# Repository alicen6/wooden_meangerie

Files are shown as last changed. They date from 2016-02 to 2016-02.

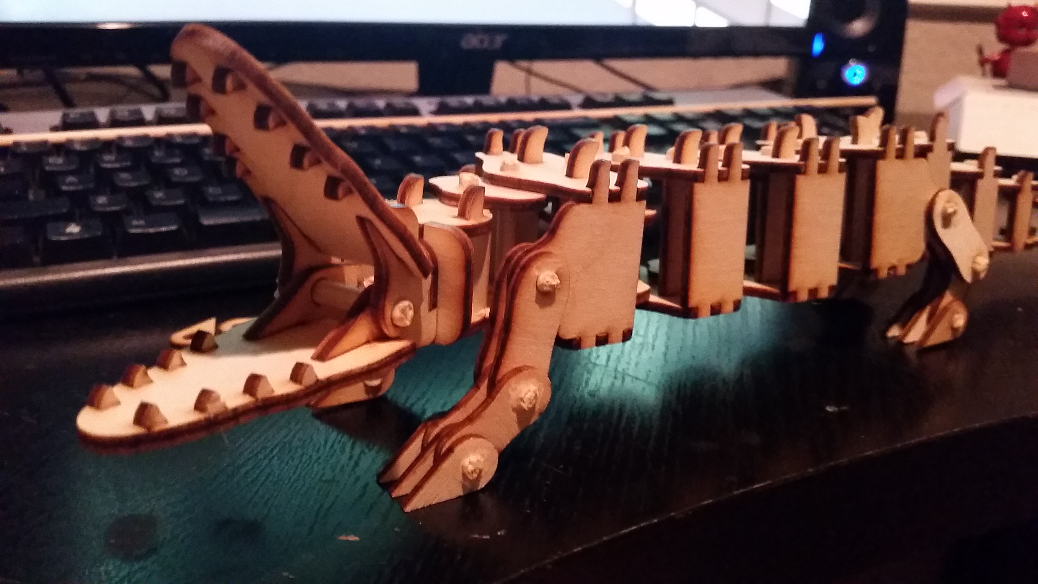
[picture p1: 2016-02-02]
images/gator.jpeg

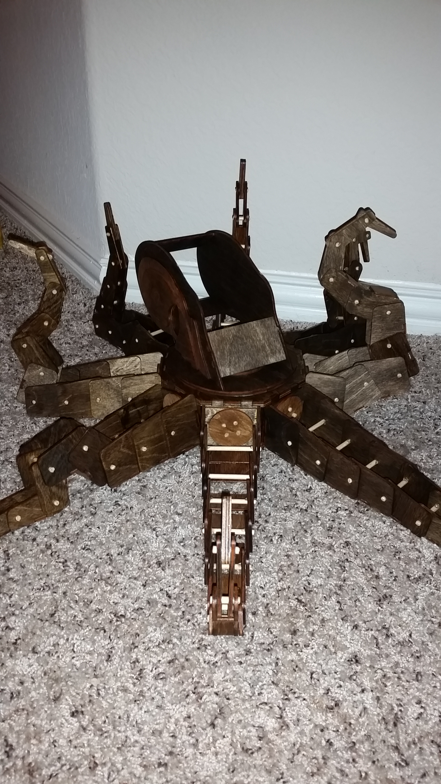
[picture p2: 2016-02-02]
images/octopus.jpg

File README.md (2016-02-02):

# Wooden Menagerie

This is a collection of files for creating articulated wooden animals. The four animals that can be created are a giraffe, an elephant, and alligator, and an octopus. All of the individual files and assemblies are within these folders.

## Materials

It is recommended to use 1/8" birch plywood or other 1/8" material for the animals. They were designed to be cut on laser cutter to reduce material waste.

The laser that they were originally created on had a bed size that would only fit 12" x 24" pieces of birch plywood, so the pre-nested files will fit onto material of that size.

These were also designed to use wooden 3/16" dowels from any Home Depot or Lowe's.

## Process

After cutting all of the pieces on a laser or other machine, it is time to assemble. For mine, I used super glue to permanently attach parts together. It is easiest to have the assembly open while putting the animal together so that you can see where different parts go.

Testing with a dry fit is encouraged, when all pieces are together, add super glue to the places that hold the dowels to keep everything together. Some areas that act as pivot points require only glue on the outer parts that touch the dowel, otherwise the pivot point won't work because they will all be glued together.

## Blog Post

http://www.alicenspurlin.com/#!Wooden-Menagerie/r2co8/5697f4e30cf20ee37c7553eb

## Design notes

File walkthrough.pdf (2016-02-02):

Wooden Menagerie Project Walkthrough

Have you ever had one of those days where you just absolutely had to make something?

I have those days far too often. I belonged to a hackerspace that had a Laser Cutter that was begging to be used. So I complied! I decided to start making articulated wooden animals that were able to be cut on the laser cutter, then assembled.

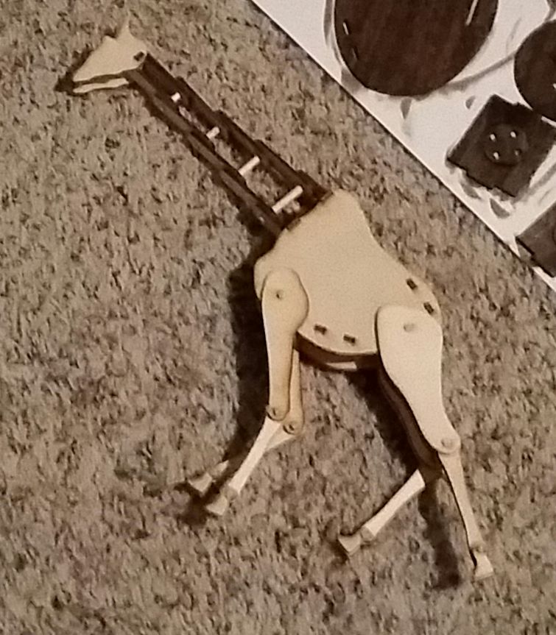
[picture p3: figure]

The first animal I began designing was a giraffe. It was fairly simple, using layers of wood to capture shafts and create joints. I used an image of a giraffe to measure and create a scale version of the animal. I also used these images to make sure that the shapes I used were accurate to the original animal.

When the pieces were cut out and I began to put them together, I found that I had made some mistakes and it didn't work as I had intended. The neck was not able to support anything and hold the head up. The pivot at the base of the head, where it connected to the neck, had not come out right in the files either.

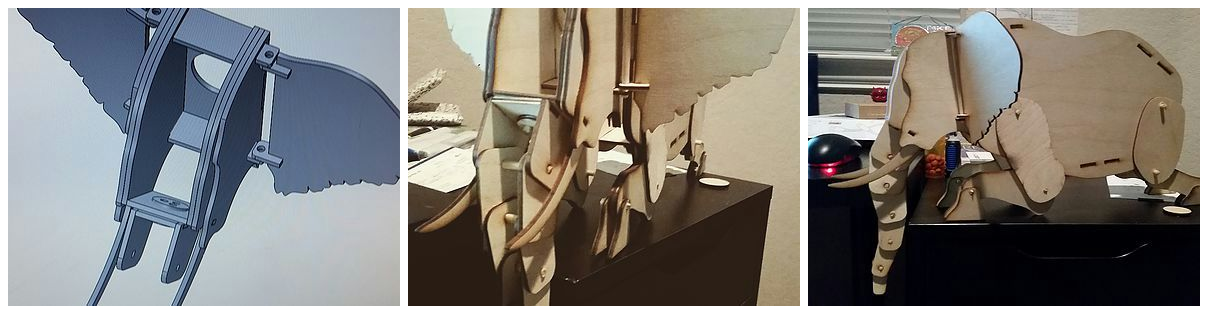
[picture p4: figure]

The second animal I designed was an elephant. The elephant was much more complex than the giraffe, with more pivots and complex build structures. The head could pivot side to side, all of the legs moved at the joints, and the ears flapped on the sides of the head. The most impressive part was the trunk, it was made of smaller and smaller sections that pivoted off one another. The trunk also pivoted at the base of the face so that it had unlimited degrees of freedom.

While assembling the elephant, the design was much more well thought out and complete, but I felt that I could still do even better.

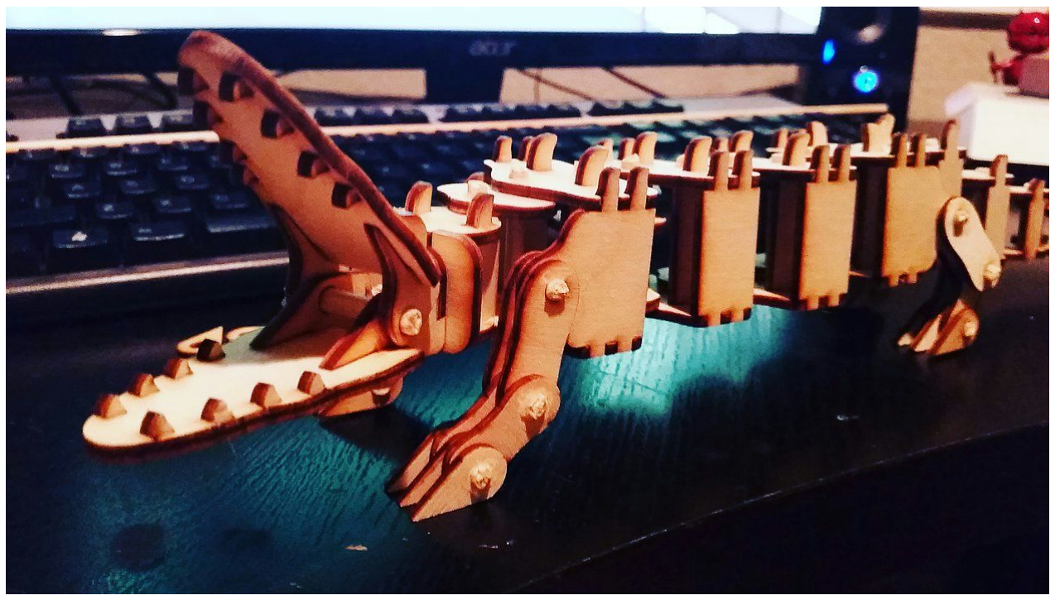
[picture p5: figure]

The third animal I designed was an alligator. The alligator was by far the most complex in the smallest package. It was made of many pieces that were similar, but would only fit together in a certain way. The entire length of the alligator was able to wiggle back and forth from the head to the tail. The legs were articulated down to the toes, and the jaw was able to open and shut.

Putting together the alligator took the longest amount of time because of the number of joints, as well as the similarity of all of the pieces.However, I still had more material I wanted to use before I moved and no longer had immediate access to the laser cutter.

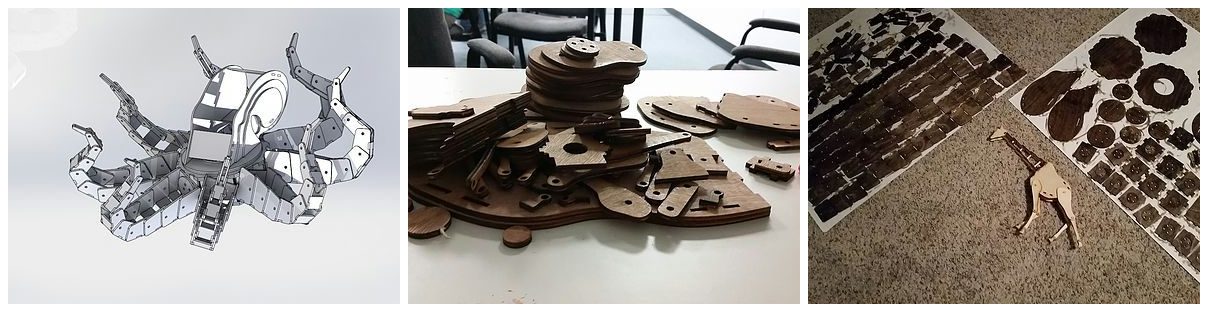
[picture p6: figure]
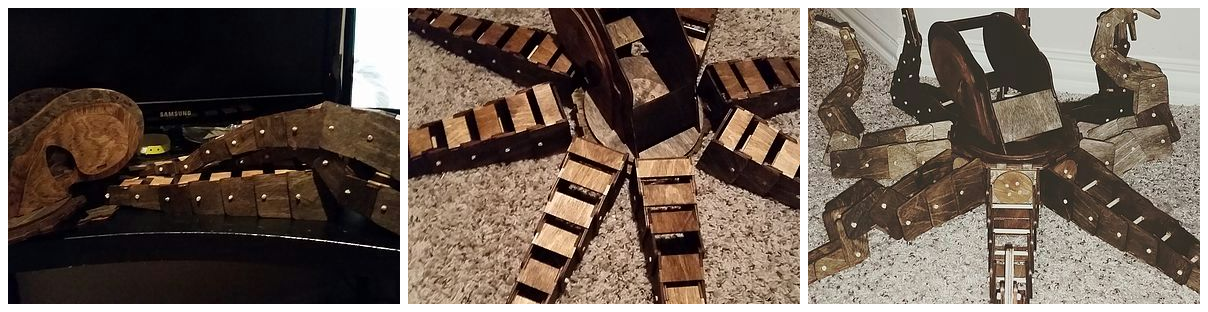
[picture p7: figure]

The fourth animal I created was an octopus. For this one, I decided to make it larger than the others. The final octopus is three feet across. The head of the octopus is able to rotate around completely. Each of the tentacles is able to rotate at the base a full 360 degrees, as well as pivot at each of the sections of the tentacles. Because I wanted to make this octopus a more finished piece than the others, I stained the parts in two different color stains before I assembled the creature together.

This project has been one of my favorites because it still has room to continue and grow, it could potentially go on forever as I learn more and more about the materials I could use and the different types of cuts and bends I can create with the laser cutter. I chose to share this project with you because I feel it shows a different side and thought process to design.

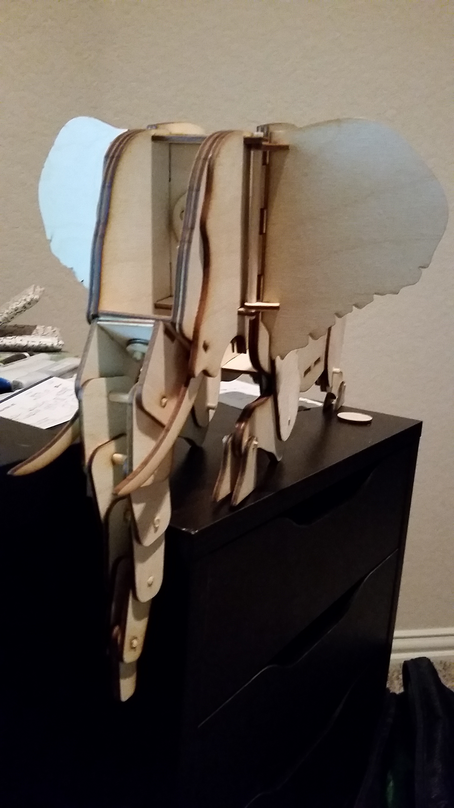
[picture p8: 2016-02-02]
images/elephant.jpg

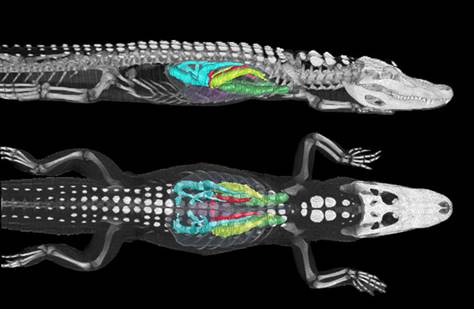
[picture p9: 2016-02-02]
alligator/alligator-CT-100114-hmed-4p.grid-6x2.jpg

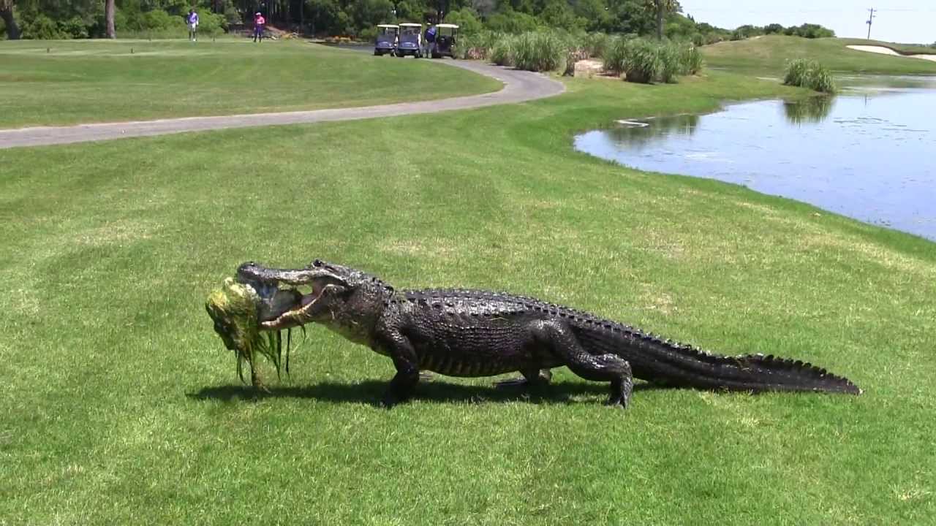
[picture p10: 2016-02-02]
alligator/maxresdefault.jpg

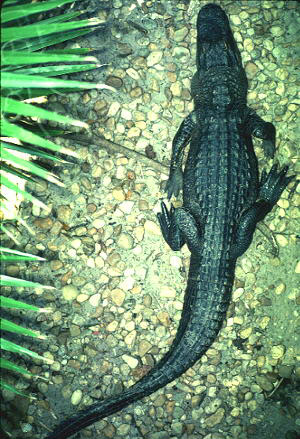
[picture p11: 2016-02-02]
alligator/!amis15.jpg

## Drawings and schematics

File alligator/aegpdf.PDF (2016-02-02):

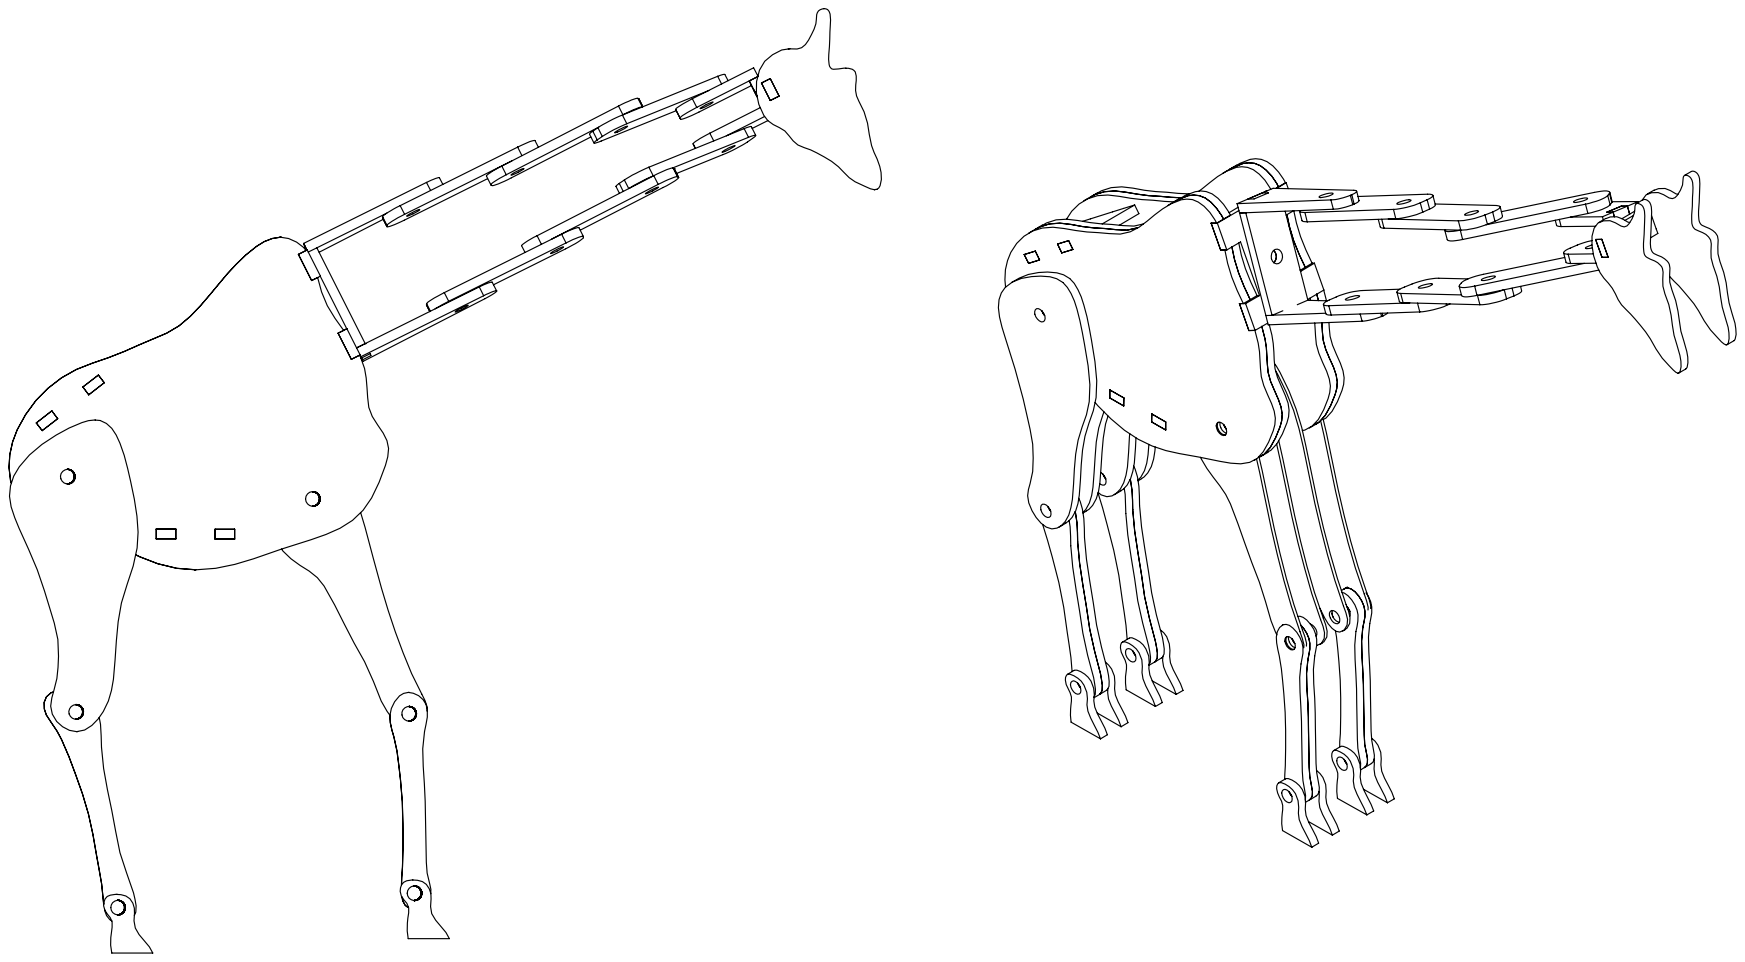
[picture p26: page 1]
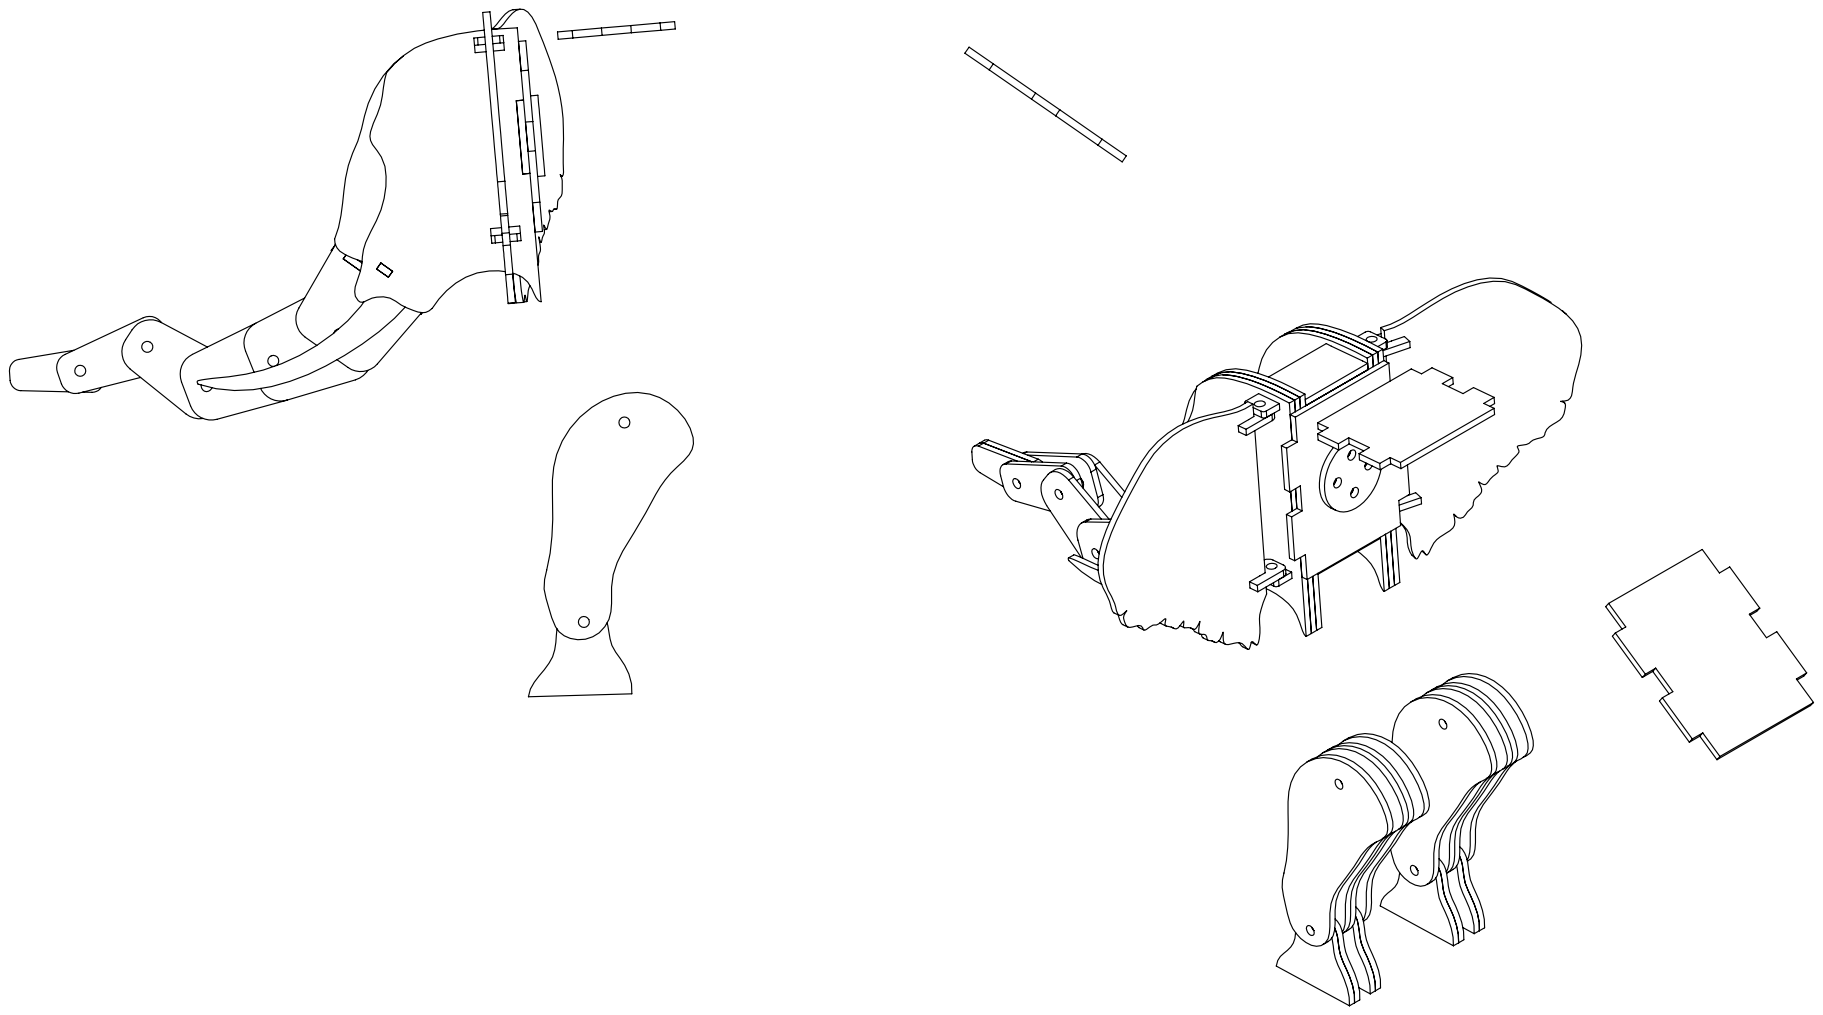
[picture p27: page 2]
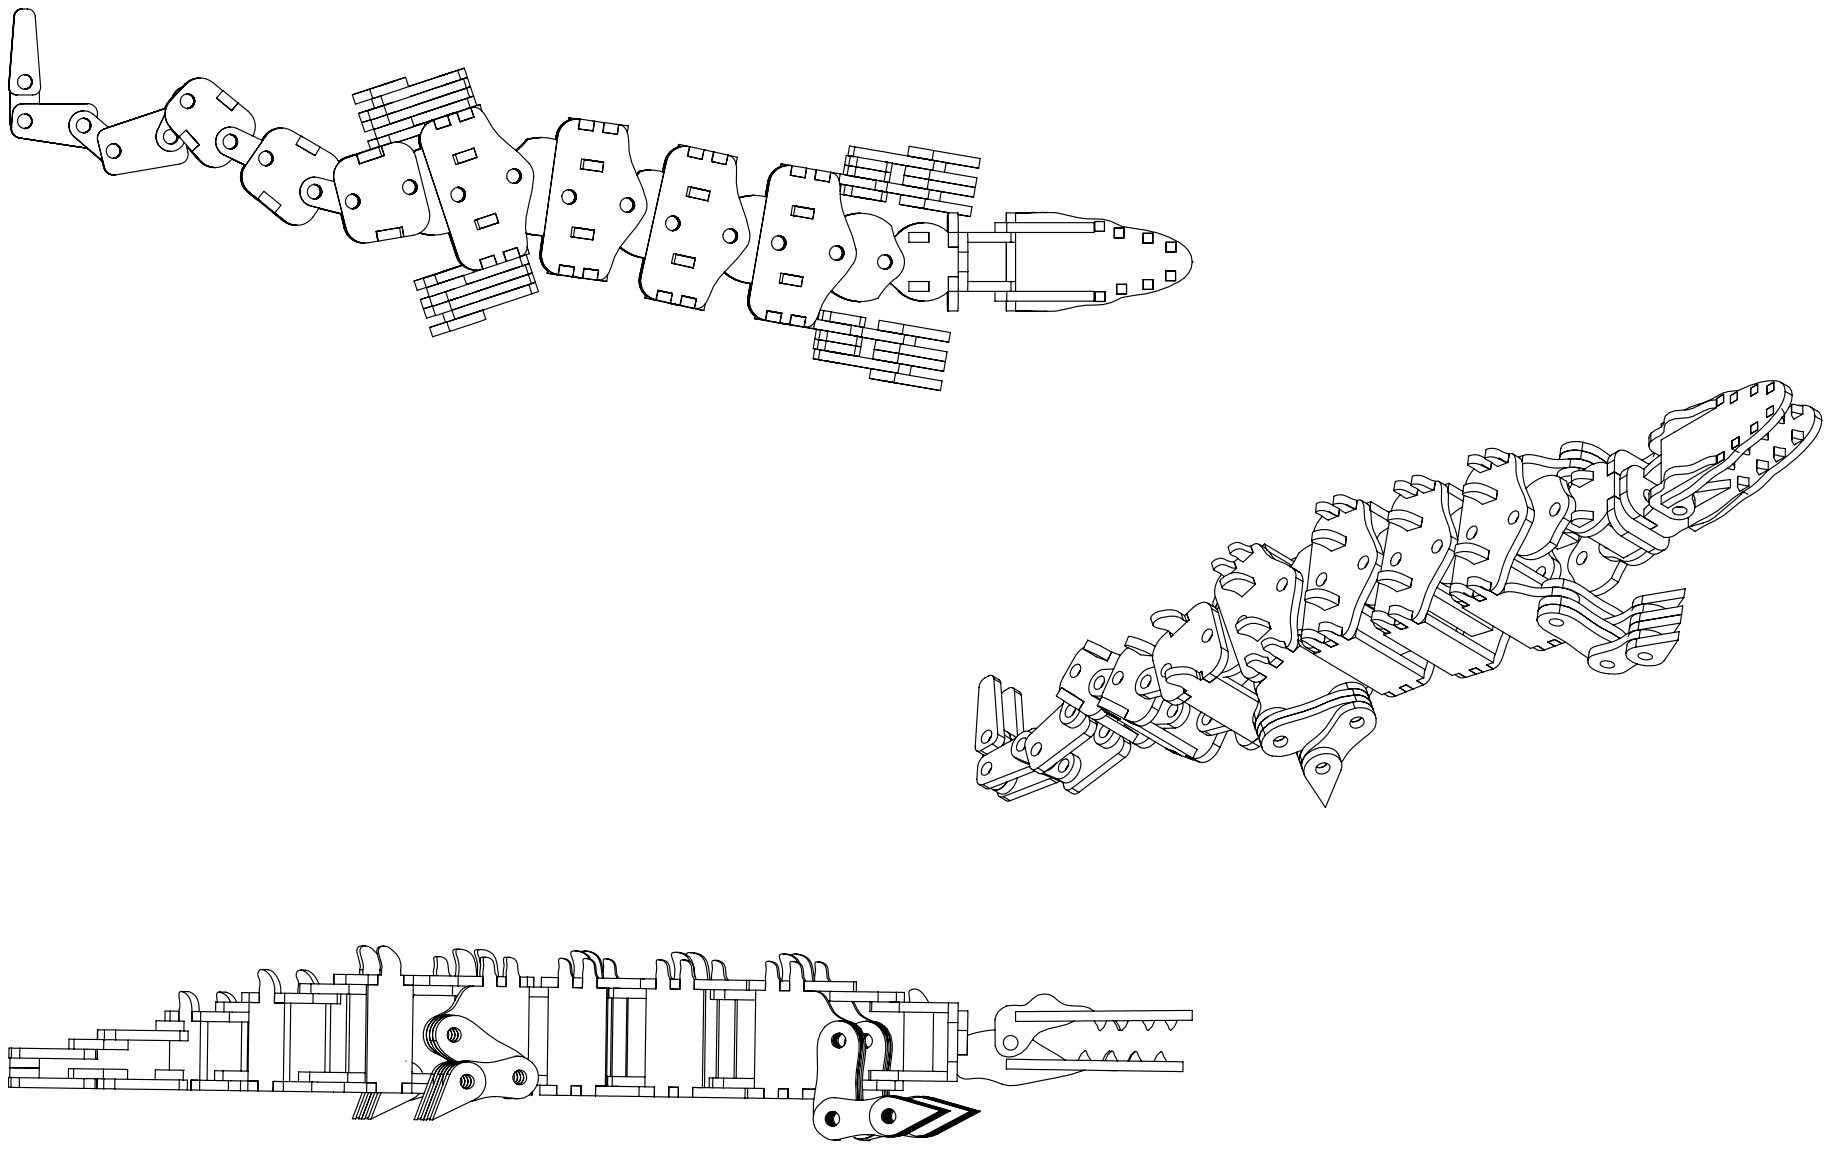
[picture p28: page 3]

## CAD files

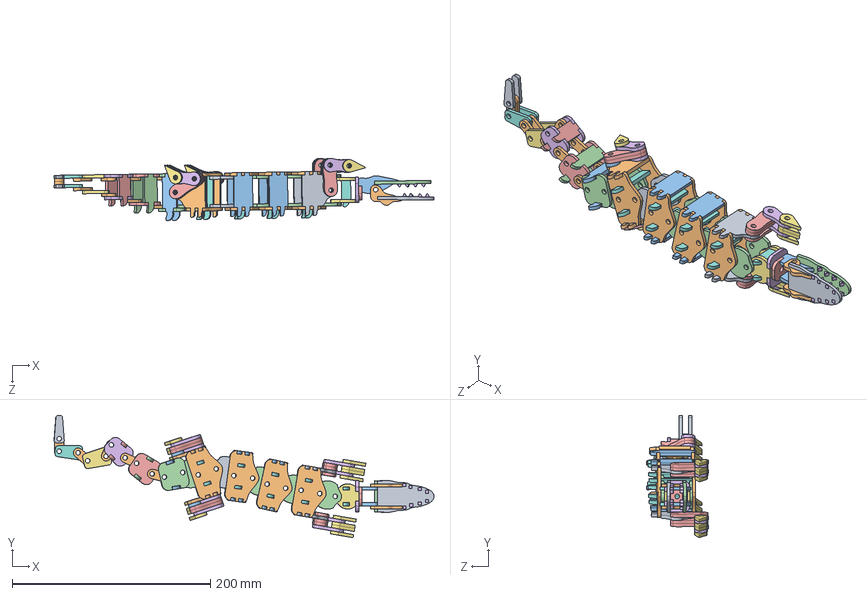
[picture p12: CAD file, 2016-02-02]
alligator/solidworks_files/a.SLDASM
383.4 x 123.5 x 63.1 mm
headtop
mouthpivot x 2
mouthpivotbottom x 2
headbottom
neckheadpivot
neckbodypivot
neckrolllink x 2
necklinksupport x 2
bodysidearm x 2
bodytoplink x 8
bodyside x 4
bodylink 2 x 8
leg1 x 10
leg2 x 8
leg3 x 16
bodysupport x 8
bodylink 3 x 2
bodysidearmrear x 2
rearlegstandoff x 2
taillink 1 x 2
taillink 2 x 2
taillink 3 x 2
taillink 4 x 2
taillink 5 x 2
taillink 6 x 2
tailconnector x 10
tailsupport 1 x 2
tailsupport 2 x 2
tailsupport 3 x 2
tooth x 16

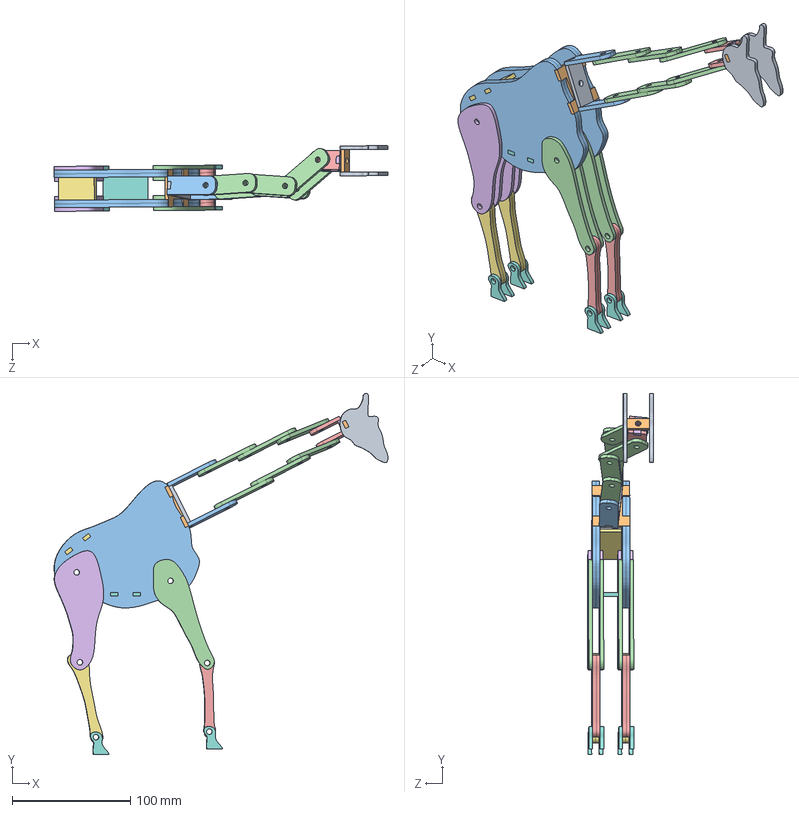
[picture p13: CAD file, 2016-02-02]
giraffe/solidworks_files/g.SLDASM
282.7 x 305.6 x 55.7 mm
head x 2
headpivot
legfront 1 x 4
legfront 2 x 4
legrear 1 x 4
legrear 2 x 4
legrear 3 x 8
neckbasepivot
neckmount
neckpiecebottom x 2
necklink x 6
neckpivottop x 2
necktoppivot2
backpan
bellypan

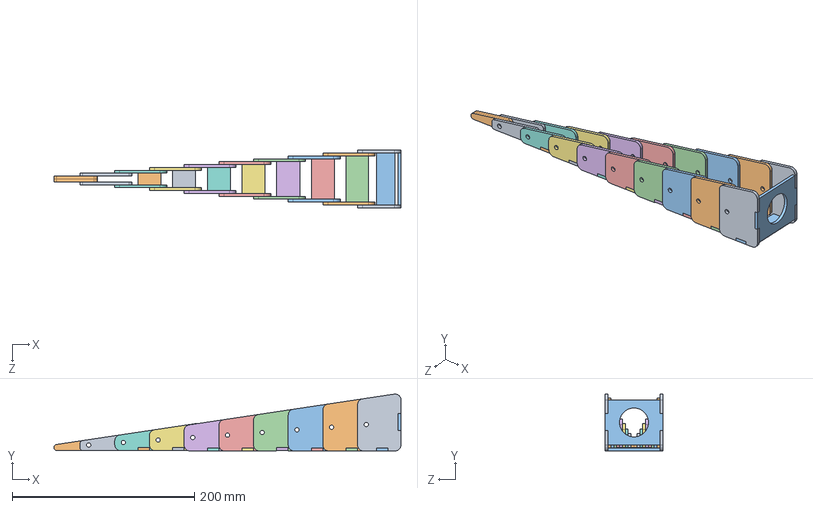
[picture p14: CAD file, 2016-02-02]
octopus/solidworks_files/tentacle.SLDASM
381.0 x 62.4 x 63.5 mm
tent1 x 2
tent2 x 2
tent3 x 2
tent4 x 2
tent5 x 2
tent6 x 2
tent7 x 2
tent8 x 2
tent9 x 2
tent10 x 2
tent1s
tent2s
tent3s
tent4s
tent5s
tent6s
tent7s
tent8s
tentattach

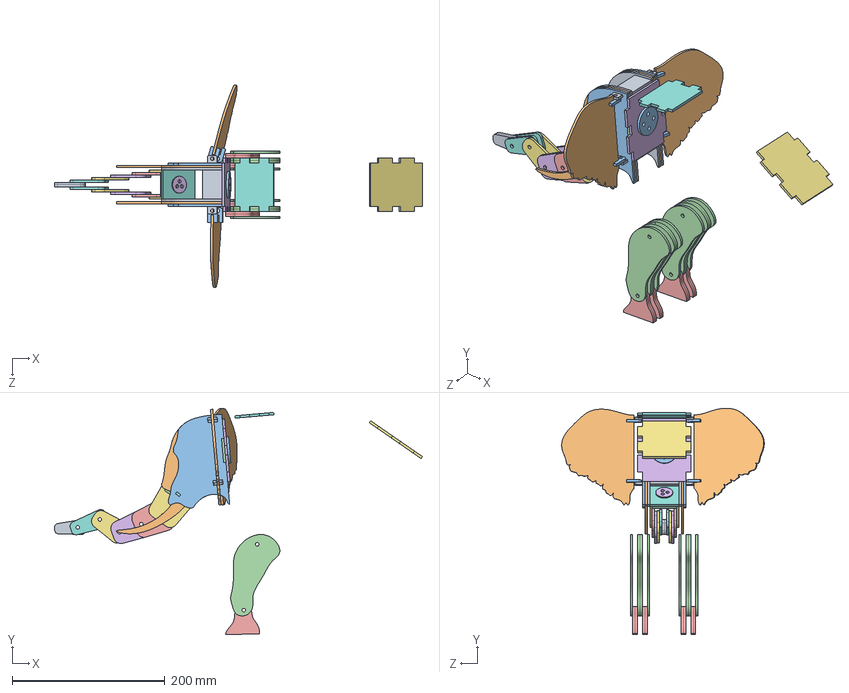
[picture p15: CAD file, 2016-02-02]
elephant/solidworks_files/e.SLDASM
482.3 x 296.7 x 265.6 mm
head1 x 2
head2 x 2
head3 x 2
trunkpivotmount
trunkbearinginner x 2
trunkbearingouter x 2
trunklink 1 x 2
trunkpivotefacemount
earmountpivot x 2
ear x 2
earlinkpivot x 4
neckpivotheadmount
trunklink 2 x 2
trunklink 3 x 2
trunklink 4 x 2
trunklink 5 x 2
trunklink 6 x 2
neckbearinginner x 2
neckbearingouter x 2
frontleg 2 x 8
legfront3 x 8
neckpivotbodymount
backpan 2
backpan 1

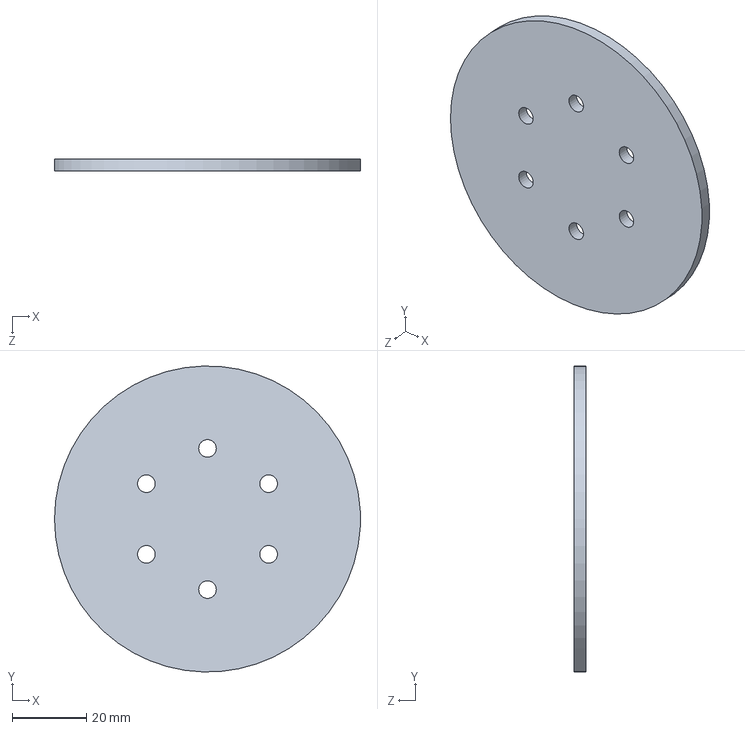
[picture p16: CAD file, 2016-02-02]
octopus/solidworks_files/mainbearingouter.SLDPRT
82.5 x 82.5 x 3.17 mm

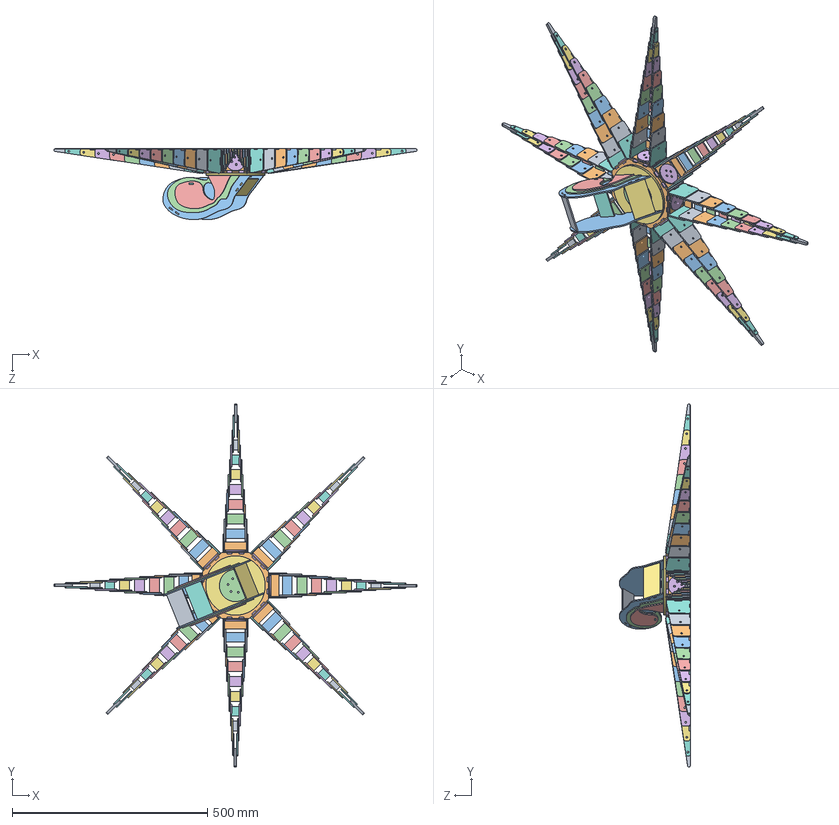
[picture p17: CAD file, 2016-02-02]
octopus/solidworks_files/o.SLDASM
930.6 x 930.6 x 182.7 mm
bodybasebottom x 2
bodybasetop x 2
head1 x 2
head2 x 2
head3 x 2
tentbaseattach x 8
headmount x 2
tent1 x 16
tent2 x 16
tent3 x 16
tent4 x 16
tent5 x 16
tent6 x 16
tent7 x 16
tent8 x 16
tent9 x 16
tent10 x 16
tent1s x 8
tent2s x 8
tent3s x 8
tent4s x 8
tent5s x 8
tent6s x 8
tent7s x 8
tent8s x 8
tentattach x 8
mainbearinginner x 4
mainbearingouter x 2
tentbearinginnner x 16
tentbearingouter x 16
head support 1
head support 2
head support 3

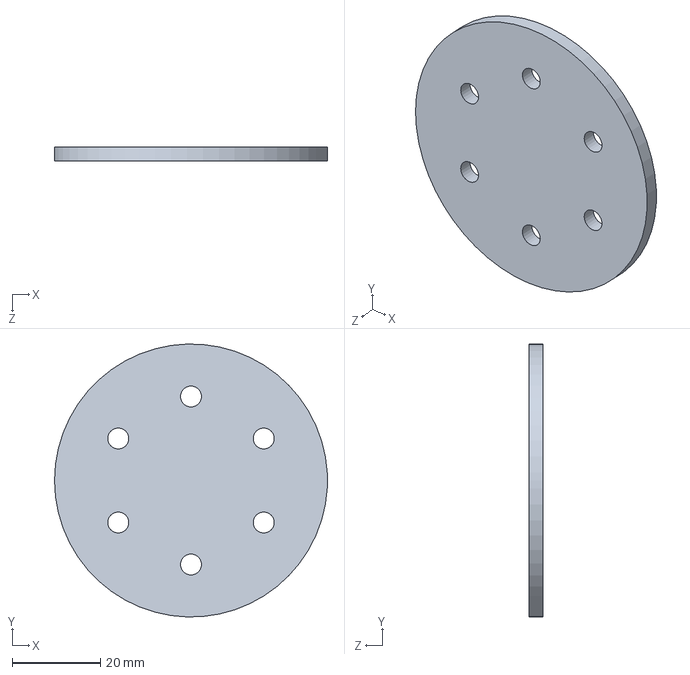
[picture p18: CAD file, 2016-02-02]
octopus/solidworks_files/mainbearinginner.SLDPRT
61.9 x 61.9 x 3.17 mm

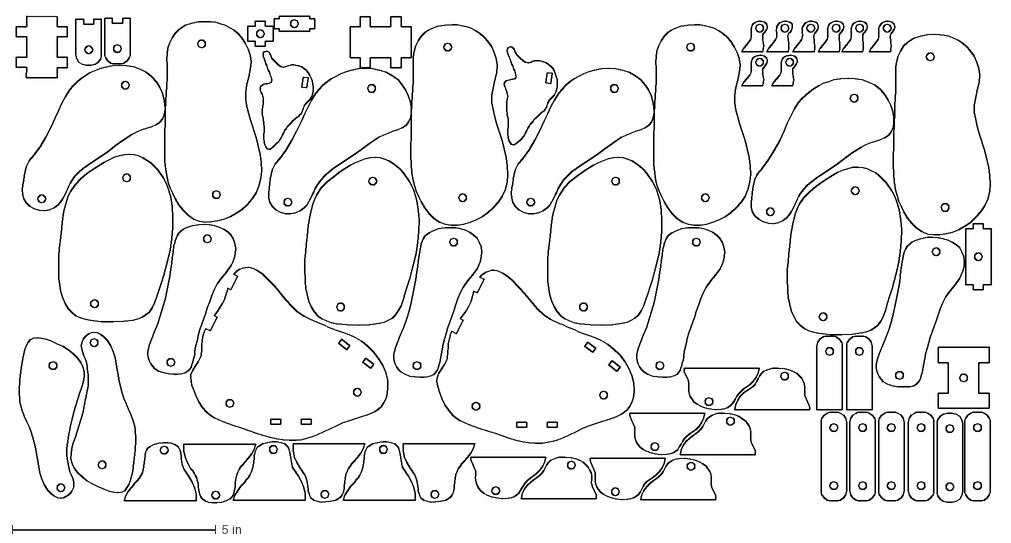
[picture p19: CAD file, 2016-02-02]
alligator/dxf_files/aeg2.dxf
24.0 x 11.9 in

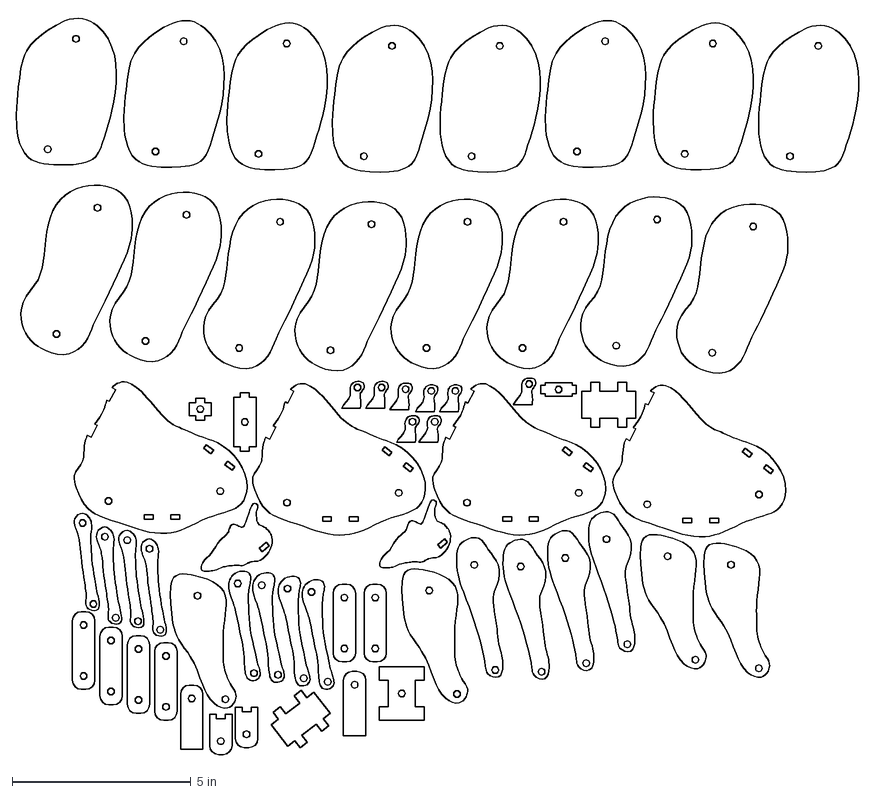
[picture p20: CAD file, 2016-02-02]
elephant/dxf_files/e2.dxf
23.6 x 20.7 in

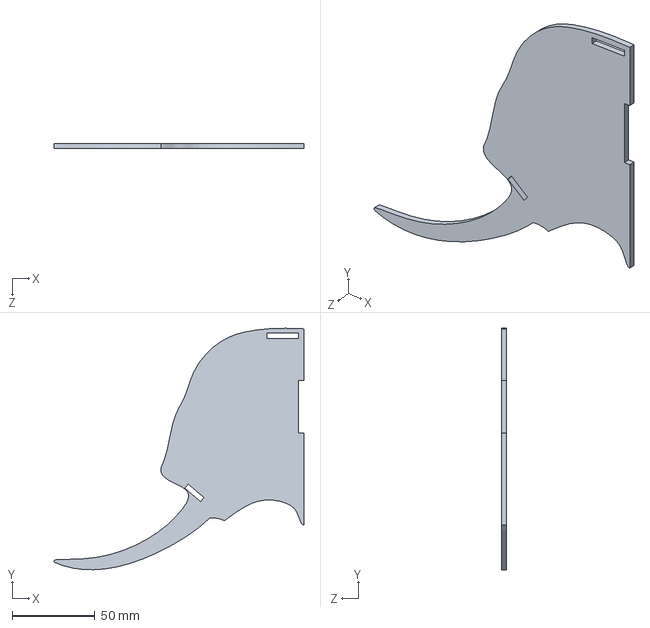
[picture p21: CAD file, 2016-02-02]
elephant/solidworks_files/head2.SLDPRT
151.0 x 145.9 x 3.17 mm

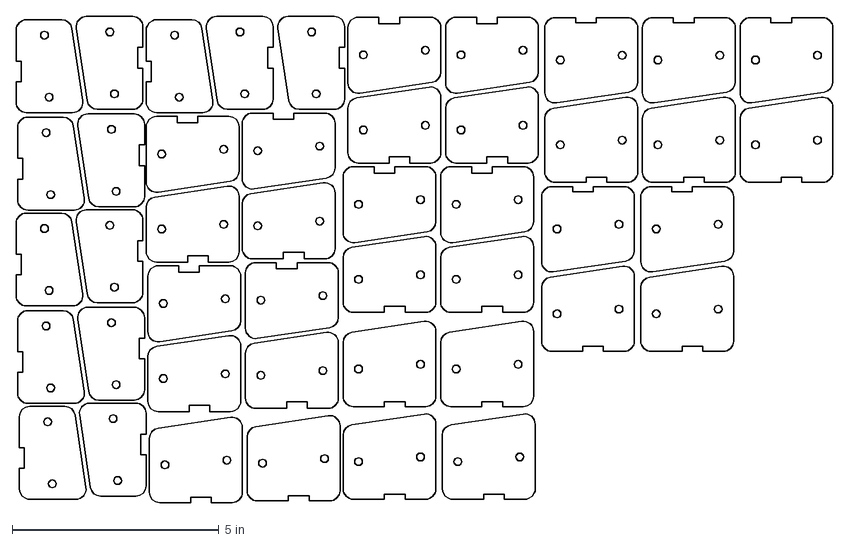
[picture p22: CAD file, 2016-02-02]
octopus/dxf_files/o5.dxf
19.8 x 11.8 in

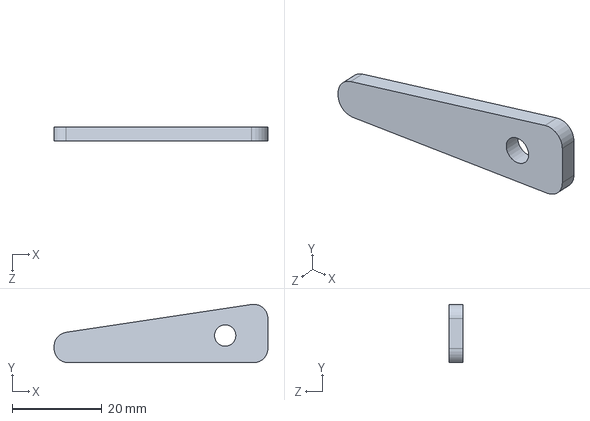
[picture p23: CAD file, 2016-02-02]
octopus/solidworks_files/tent10.SLDPRT
47.6 x 13.0 x 3.17 mm

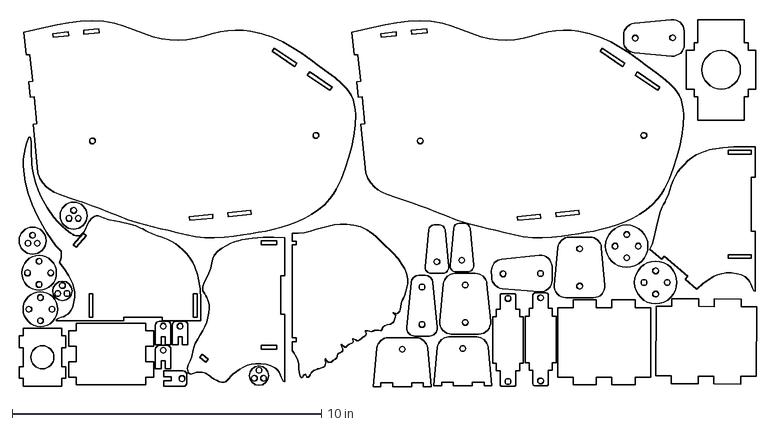
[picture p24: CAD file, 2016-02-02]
alligator/dxf_files/aeg1.dxf
24.0 x 12.0 in

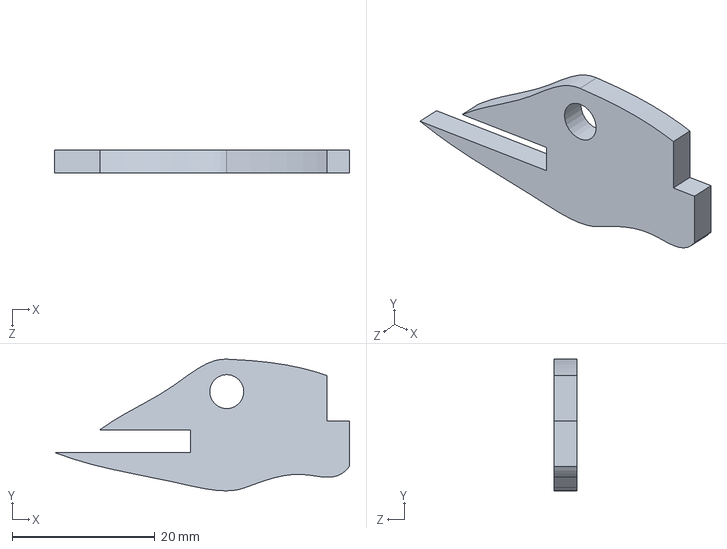
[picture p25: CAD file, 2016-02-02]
alligator/solidworks_files/mouthpivotbottom.SLDPRT
41.3 x 18.4 x 3.17 mm

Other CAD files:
elephant/dxf_files/e1.dxf
elephant/solidworks_files/ear.SLDPRT
giraffe/solidworks_files/g nest.SLDPRT
octopus/dxf_files/onest.dxf
alligator/aeg.dwg
alligator/aeg1.dwg
alligator/aeg2.dwg
alligator/aeg3.dwg
alligator/aeg4.dwg
alligator/dxf_files/aeg.dxf
alligator/dxf_files/aeg3.dxf
alligator/dxf_files/aeg4.dxf
alligator/dxf_files/bodylink 2.DXF
alligator/dxf_files/bodylink 3.DXF
alligator/dxf_files/bodyside.DXF
alligator/dxf_files/bodysidearm.DXF
alligator/dxf_files/bodysidearmrear.DXF
alligator/dxf_files/bodysupport.DXF
alligator/dxf_files/bodytoplink.DXF
alligator/dxf_files/headbottom.DXF
alligator/dxf_files/headtop.DXF
alligator/dxf_files/leg1.DXF
alligator/dxf_files/leg2.DXF
alligator/dxf_files/leg3.DXF
alligator/dxf_files/mouthpivot.DXF
alligator/dxf_files/mouthpivotbottom.DXF
alligator/dxf_files/neckbodypivot.DXF
alligator/dxf_files/neckheadpivot.DXF
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
